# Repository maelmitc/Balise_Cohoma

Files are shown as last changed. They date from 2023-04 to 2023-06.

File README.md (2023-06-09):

# $${\color{black}Balise \space \color{black}Cohoma}$$

* CHARBONNIER Maëna
* MITCHEL Maël
* NGUYEN Denis
* SALOT Robin
* TESTUZ Lauriane

## $${\color{black}Présentation \space \color{black}du \space \color{black}{projet}}$$

Ce projet est en collaboration avec des deuxièmes années qui participent au projet Cohoma, pour l'armée de terre. Ce projet
est une compétition entre différentes écoles d'ingénieurs. Il consiste en la création d'un robot autonome s'adaptant à tout type de terrains. Ce robot doit lâcher des balises sur son chemin, elles ont pour but de le localiser. C'est ce sur quoi nous avons travaillé. 
   
Une LED RGB est utilisée afin de montrer le niveau de batterie de la balise (vert: pleine charge, jaune: à moitié chargée et rouge: déchargée). Quatre LEDs bleues sont également utilisées afin de déterminer le niveau de connexion Internet de la balise. Il y a également un capteur infrarouge qui permet de communiquer avec le rover afin d'allumer la batterie. Enfin, on utilise un convertisseur Buck-Boost, qui est une alimentation à découplage qui convertit une tension continue en une autre tension continue de plus faible ou de plus grande valeur, mais de polarité inverse.

## $${\color{black}Cahier \space \color{black}des \space \color{black}{charges}}$$

* Rendre visible le niveau de batteries de la balise (sur la balise).
* Rendre visible le niveau de réception WIFI de la balise (sur la balise).
* Communication infrarouge entre une télécommande et la balise.
* Communication infrarouge entre le rover et la balise dans le but d'allumer la balise après lors de l'éjection.
* Alimenter la balise.

## $${\color{black}Datasheet}$$

* [Buck / Boost ](https://www.farnell.com/datasheets/1999134.pdf)
* [Diode (Buck) (1N4148)](https://4donline.ihs.com/images/VipMasterIC/IC/DIOD/DIOD-S-A0001754954/DIOD-S-A0001754954-1.pdf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)
* [Diode Schottky (FSV340AF)](https://www.mouser.fr/datasheet/2/308/FSV340AF_D-1810142.pdf)
* [Capteur IR TFBS4650](https://www.vishay.com/docs/84672/tfbs4650.pdf)
* [Interface USB/UART(CY7C64225-28PVXCT)](https://www.mouser.fr/datasheet/2/196/CYPR_S_A0003298042_1-3003715.pdf)
* [Encodeur/Decodeur IrDA MCP2120-I/SL ](https://docs.rs-online.com/4edb/0900766b814ada76.pdf)
* [Quartz pour Encodeur/Decodeur IrDA ABLS-7.3728MHZ-20-B-3-H-T ](https://www.mouser.fr/datasheet/2/3/abls-1664338.pdf)
* [Récepteur IrDA TSOP75338TT](https://www.mouser.fr/datasheet/2/427/tsop753-1767096.pdf)
* [Emetteur IrDA VSML3710-GS18](https://www.mouser.fr/datasheet/2/427/vsml3710-1766511.pdf)
* [Processeur STM32L412KBT6](https://www.mouser.fr/datasheet/2/389/stm32l412c8-1851177.pdf)
* [Quartz pour STM32 ABLS-16.000MHZ-20-B-3-H-T:](https://www.mouser.fr/datasheet/2/3/abls-1664338.pdf)
* [Led bleu (niveau de réception) : MP008276]( https://www.farnell.com/datasheets/3497873.pdf)
* [Led RGB (niveau batterie) : 5988G10313F ](https://www.mouser.fr/datasheet/2/109/C18481B-2944388.pdf)
* [Driver de LED I2C : PCA9685PW,118 ]( https://www.mouser.fr/datasheet/2/302/PCA9685-1127478.pdf)

## $${\color{black}Déroulement \space \color{black}du \space \color{black}{projet}}$$

### Software :

L'objectif du logiciel développé est le traitement des données du routeur et de la batterie et la commande du <em>driver</em> LED. Le code a été développé en C. Le code est implémenté sur un processeur STM32 L412KBT6. En fonction des données reçues, le logiciel commande les LEDs, en particulier en fonction du niveau de batterie disponible. Le driver de LEDs, relié à quatre LEDs bleues et une LED RGB est connecté en I2C avec le processeur STM32.

* [Architecture <em>software</em>](Software/[CoHoMa]BeaconSoftwareArchitecture.drawio) (originale, modifiée depuis)
* [Code](Software/CHMBeaconB.zip)

#### Batterie
Selon le niveau de batterie calculé, 1 à 4 Blue LEDs sont allumées
* 75% : 4 LEDs activées
* 50% : 3 LEDs activées
* 25% : 2 LEDs activées
* 10% : 1 LED activée
On utilise une connexion I²C pour lier le STM32 au <em>driver</em> LED.

#### Routeur/IR
On utilise une LED RGB pour témoigner de la qualité de la connexion.
En fonctionnement normal, on utilise 3 couleurs : rouge (signal faible), vert (signal moyen), bleu (signal fort).

#### Problèmes rencontrés lors du développement :
* Longue lecture des fiches techniques des composants utilisés
* Recherche et étude d'un algorithme pour déterminer le niveau de batterie (SOC Algorithm)
* Lien entre la partie <em>hardware</em> et <em>software</em>, en particulier le lien avec la batterie/le niveau de charge

D'un point de vue personnel, je juge avoir sous-estimé la quantité de travail à fournir dans la partie <em>software</em>, trop importante pour une seule personne.

### Hardware - PCB Leds:

La version finale de mon [PCB](Hardware/PCB_LEDs/PCB_LEDs.kicad_sch_copie.kicad_pro).

#### Composants utilisés : 

Type de produit | Empreinte | Nombre 
--- | --- | ---
Driver de LEDs | Package_STO:TSSOP-28_4.4x9.7mm_P0.65mm | 1
LED bleue | LED_SMD:LED_0603_1608Metric_Pad1.05x0.95mm_HandSolder | 4 
LED RGB | LED_SMD:LED_Avago_PLCC6_3x2.8mm | 1
Résistance (100Ω et 150Ω)| Resistor_SMD:R_0603_1608Metric_Pad0.98x0.95mm_HandSolder | 7
Connecteur 01x05 | Connector_JST:JST_XH_B5B-XH-A_1x05_P2.50mm_Vertical | 1

#### Utilité des composants :

* Driver de LEDs : pilote les LEDs.
* LEDs bleues : montrent le niveau de connexion Wifi sur la balise. Plus le nombre de LEDs allumées est important, plus la connexion internet est bonne. 
* LED RGB : montre le niveau de batterie de la balise. Si la LED est verte, la balise est entièrement chargée ; jaune, à moitié chargée ; rouge, déchargée.
* Résistances : permettent de limiter le courant qui traverse les LEDs.
* Connecteur : permet de faire communiquer le driver de LEDs avec l’extérieur. Il est composé de cinq sorties : une d'alimentation et une de masse, mais également d'une sortie SDA (Serial Data Line), d'une sortie SCL (Serial Clock Line) et d'une sortie output enable, qui permet d’activer ou de désactiver les sorties de LEDs, en fonction des besoins.

#### Choix des résistances : 

Le driver de LEDs est alimenté par une tension de 5V. La tension maximum que peuvent recevoir les LEDs est d’environ 3V. Or, puisqu’on a un courant de 25 mA qui doit traverser les LEDs, on en conclut que la résistance qui doit être ajoutée afin de limiter la tension est de 100Ω. EN ce qui concerne la LED RGB, la diode rouge supporte une tension moins importante que les diodes jaune et verte. Sa résistance doit donc être supérieure à celles des diodes jaune et verte. C’est pourquoi, on ajoute une résistance de 150Ω.

#### Problèmes rencontrés lors de la fabrication de ce PCB : 

En ce qui concerne les LEDs bleues, il n'y a pas de problème, elles s'allument correctement. En revanche, cette partie comporte un principal problème : à cause d'une mauvaise connexion des pins de la LED RGB, on s'est rendu compte que seule la diode verte s'allume, les diodes jaune et rouge ne fonctionnent pas. Il faut prendre garde à ne pas se tromper entre l'anode et la cathode des diodes, pour éviter que l'erreur ne se reproduise. 

### Hardware - PCB IR :

La version finale de mon [PCB](Hardware/PCB_IR/cohoma.kicad_pro).

#### Composants utilisés : 

Type de produit | Empreinte | Nombre 
--- | --- | ---
Décodeur | Package_SO:SOIC-14_3.9x8.7mm_P1.27mm | 1
Récepteur Infrarouge | Package_SO:TSOP753TT (empreinte que nous avons créée) | 1
Quartz | Crystal:Crystal_SMD_7050-2Pin_7.0x5.0mm | 1
Condensateur (20 pF et 100 nF)| Capacitor_SMD:C_0603_1608Metric_Pad1.08x0.95mm_HandSolder | 3
Connecteur 01x03 | Connector_PinHeader_1.27mm:PinHeader_1x03_P1.27mm_Horizontal | 1 

Ce PCB se compose de plusieurs parties:

#### Récepteur IR:
Le récepteur IR reçoit un signal provenant d'un émetteur IR. Il renvoie alors RXIR à l'encodeur/décodeur dans le but que le signal soit décodé.
Afin d'éviter les fluctuations de tensions, il était recommandé par la datasheet, lorsque Vs<2.8 V d'utiliser une résistance et un condensateur. Ce n'est ici pas le cas, cependant, afin d'éviter tout risque, un condensateur de 100 nF a tout de même été ajouté.

#### Encodeur/Décodeur:
Dans le cadre de ce projet, ce composant a été utilisé uniquement comme un décodeur. Il reçoit RXIR, le décode et renvoie UART_RX au microcontrôleur (via le connecteur).
En effet, pour être compris par le microcontrôleur, le signal doit être en UART.

Les "BAUD" permettent de modifier la vitesse de transmission. Ils sont tous les trois mis à la masse ici, ce qui équivaut à les mettre à 0.

#### Quartz:
Le quartz sert d'horloge. Il est ici accompagné de deux condensateurs qui permettent de "lisser" afin que l'horloge soit vraiment régulière.

#### Difficultés rencontrées lors de la fabrication de ce PCB :
* Trouver les schematics correspondants au projet (pour plusieurs composants, elles n'existaient pas sur Kicad: il a donc été nécessaire de les trouver, les télécharger, puis les importer sur Kicad).
* La datasheet du quartz ne permettait pas de connaître la schematic associée, il fallait effectuer d'autres recherches.
* De même pour les empreintes de certains composants, il fallait alors trouver une empreinte très proche, ou bien créer l'empreinte dans certains cas.
* Rendre le PCB le plus petit possible tout en respectant une contrainte: les deux condensateurs associés au Quartz devaient être aussi proche que possible de ce dernier.
* Problèmes rencontrés lors de la soudure liés à une mauvaise empreinte ( qui a été corrigée sur la dernière version du PCB).

### Hardware - PCB Buck-Boost:

La version finale de notre [PCB](Hardware/PCB_BuckBoost/pcb_v3/pcb_v3.kicad_pro).

#### Composants utilisés : 

Type de produit | Empreinte | Nombre 
--- | --- | ---
Diode| Diode_SMD:D_SOD-123F | 1
Diode| Diode_SMD:D_SOD-323F | 1
PS1| Footprints_Balise:PS1 | 1
Régulateur Buck/Boost | Package_SO:SOIC-8-1EP_3.9x4.9mm_P1.27mm_EP2.29x3mm | 2
Condensateur polarisé (330 uF)| Capacitor_SMD:CP_Elec_10x10.5 | 2
Condensateur polarisé (100 uF)| Capacitor_SMD:CP_Elec_6.3x7.7 | 1
Condensateur polarisé (22 uF)| Capacitor_SMD:CP_Elec_5x5.4 | 1
Condensateur (2.2 uF, 1 uF et 0.47 nF)| Capacitor_SMD:C_0603_1608Metric_Pad1.08x0.95mm_HandSolder | 6
LED bleue | LED_SMD:LED_0603_1608Metric_Pad1.05x0.95mm_HandSolder | 4 
Inductance (100 uH)| Inductor_SMD:L_Wuerth_WE-PD-Typ-LS | 2
Résistance | Resistor_SMD:R_0603_1608Metric_Pad0.98x0.95mm_HandSolder | 11
Diode Schottky | Footprints_Balise:Diode_Schottky (empreinte créée)| 2
Connecteur 01x02 | Connector_JST:JST_XH_B2B-XH-A_1x02_P2.50mm_Vertical | 4

#### Utilité des composants
* LEDs bleues : témoignent du bon fonctionnement de l'alimentation
* Diodes / Diode Schottky : permettent les différents états de commutation du régulateur
* Régulateur à découpage : gère le découpage (via le rapport cyclique) de la tension en fonction des différents états. Les régulateurs sont au nombre de deux, chacun est monté différemment, permettant le passage au mode Buck ou Boost.
* PS1 : régule la tension

#### Choix des composants     
Les composants (autre que ceux imposés) ont été sélectionnés en fonction des datasheets des montages Buck et Boost et des composants passifs disponibles à l'ENSEA. Pour ce qui est des condensateurs, des condensateurs classiques ou polarisés ont été choisi en fonction de la valeur des capacités indiquées sur la datasheet (au dessus de 10 uF, on choisit un condensateur polarisé).

#### Explication du fonctionnement des régulateurs à découplage  
Un régulateur de découplage est un type de régulateur de tension qui utilise des composants électroniques commutés (transistors, inductances, condensateurs) pour convertir l'énergie de manière efficace. 

Régulation de la tension d'entrée : Le régulateur de découplage commence par réguler et contrôler la tension d'entrée, celle-ci pouvant être supérieure ou inférieure à la tension de sortie souhaitée, à l'aide de composants électroniques commutés.

Conversion d'énergie : L'énergie est efficacement convertie en utilisant un interrupteur électronique, généralement un transistor, pour commuter rapidement entre les états "on" et "off". Il est possible de réduire les pertes d'énergie et d'améliorer l'efficacité globale du régulateur grâce à cette commutation.

Stockage de l'énergie : Pendant la commutation, l'énergie est stockée dans une inductance (bobine) lors de l'état "on" de l'interrupteur et est libérée lors de l'état "off". Cela permet de réguler et de maintenir la tension de sortie constante malgré les variations de la tension d'entrée ou de la charge.

Filtrage : Le régulateur de découplage utilise également des condensateurs pour filtrer les fluctuations résiduelles de la tension de sortie et pour fournir une alimentation stable et régulée.

#### Difficultés rencontrées lors de la fabrication de ce PCB : 
* Repérer sur la datasheet les montages buck et boost qui correspondaient au projet.
* Choisir des empreintes des condensateurs et des inductances adaptées à la situations (exemple : condensateurs polarisés).
* Assigner (voire créer) les bonnes empreintes car elles n'étaient pas toujours disponibles sur Kicad.  
* Agencer les composants afin d'obtenir un PCB le plus petit possible.
* Placer les composants traversés par une forte tension de manière optimale (ils devaient être proches des régulateurs à découpage).
* Il fallait imposer un courant de sortie de 100 mA, ce qui n'était possible que si la balise était complète. Or, ce n'était pas le cas, puisque nous n'avions que le PCB. Nous avons donc dû rajouter deux résistances en parallèle à un condensateur polarisé.
* Choisir une largeur de piste suffisante en fonction du courant qui traversait les différents composants. 
* Augmenter le nombre de vias car ils ne fonctionnaient pas toujours.
* Certaines pastilles de cuivres n'étaient pas connectés à la masse, une erreur lors de la conception du PCB sur Kicad.

## $${\color{black}Impact \space \color{black}environnemental}$$

### $${\color{green}Expliquer \space \color{green}les \space \color{green}{critères} \space \color{green}de \space \color{green}choix \space \color{green}du \space \color{green}mode \space \color{green}d'alimentation \space \color{green}de \space \color{green}votre \space \color{green}{projet}}$$

Notre projet exigeait déjà un cahier des charges précis à respecter. En effet, la plupart des composants, y compris l'alimentation Buck-Boost, étaient imposés. Cependant, on peut tout de même se demander pourquoi c'est une alimentation à découpage qui à été choisie plutôt qu'une alimentation linéaire. En effet, l'alimentation à découpage possède un rendement bien plus élevé (et consomme donc moins d'énergie) que l'amplificateur linéaire grâce à son fonctionnement "alterné" entre différents états de commutations. Cette meilleure efficacité énergétique est principalement due à leur principe de fonctionnement différent. Dans un régulateur linéaire, la tension excédentaire est dissipée sous forme de chaleur par un transistor de régulation. Cela signifie que la différence de tension entre l'entrée et la sortie du régulateur est convertie en chaleur, ce qui entraîne une perte d'énergie importante. Par conséquent, les régulateurs linéaires ont généralement une efficacité relativement faible, en particulier lorsque la différence de tension entre l'entrée et la sortie est importante. 

En revanche, les régulateurs de découplage utilisent des composants électroniques commutés, tels que des transistors MOSFET et des inductances, pour réguler la tension de sortie. Ces composants commutent rapidement entre les états "on" et "off", ce qui permet de minimiser les pertes d'énergie. Lorsque le transistor est en état "on", il présente une résistance très faible, ce qui réduit les pertes de puissance. Lorsque le transistor est en état "off", l'inductance stocke l'énergie et la restitue lors de l'état "on" suivant, ce qui permet de maintenir une tension de sortie constante.En conséquence, les régulateurs de découplage ont une efficacité énergétique beaucoup plus élevée que les régulateurs linéaires. Une plus grande quantité d'énergie est transférée du côté de l'entrée vers le côté de la sortie sans être dissipée sous forme de chaleur. De plus, en raison du rapport cyclique, le transformateur à l'intérieur de l'alimentation peut être très petit, réalisant ainsi la miniaturisation de la taille de l'alimentation tout en permettant également l'utilisation normale de l'alimentation. 

Il est à noter que dans certains cas (dans d'autres projets par exemple), l'utilisation des régulateurs linéaire est préférable : 
* Moins sensible aux variations de la tension d'entrée,
* Coût moins élevé,
* Meilleure performance en terme de réduction de bruit et des interférences électromagnétique, 
* Moins complexe
* Réglage plus fin de la sortie.

### $${\color{green}Votre \space \color{green}projet \space \color{green}favorise-t-il \space \color{green}une \space \color{green}utilisation \space \color{green}judicieuse \space \color{green}et \space \color{green}rationnelle \space \color{green}de \space \color{green}l'énergie, \space \color{green}en \space \color{green}minimisant \space \color{green}{les}}$$

### $${\color{green}impacts \space \color{green}de \space \color{green}sa \space \color{green}production, \space \color{green}de \space \color{green}sa \space \color{green}distribution \space \color{green}et \space \color{green}de \space \color{green}sa \space \color{green}{consommation?}}$$
 
La plupart des composants étant imposés, nous avons eu peu de marge de manoeuvre. Nous avons donc porté une attention toute particulière à la taille des PCBs conçus. En effet, ces derniers devaient être les plus petits possibles, afin de ne pas gaspiller de matériaux. De plus, les PCBs ayant été réalisés sur place, leur impact environnemental dû aux transports était minime, les composants étant déjà à l'école.
 
Pour ce qui est des LEDs présentes sur le projet, elles ne s’allument que lorsque le module qui leur est associé est sollicité. Ainsi il n'y a pas d'énergie utilisée inutilement. De plus, nous nous sommes assurés qu’aucun composant ne consomme plus d’énergie que celle nécessaire à son bon fonctionnement.

Cependant, si l’on s’intéresse au projet de manière plus large, son impact est plus important que ce que nous avons décrit précédemment. En effet, plusieurs écoles sont en compétition dans la réalisation de ce projet pour ne sélectionner que le meilleur. L’impact aurait été moins important si une seule équipe d’ingénieurs professionnels s’en était chargée. Néanmoins, cette compétition entre écoles encourage chacun des participants à réaliser le projet le plus efficace et propre possible dans l’espoir d’être sélectionnés.

## $${\color{black}Conclusion}$$

Nous avons manqué de temps pour atteindre tous nos objectifs. Cependant, si nous pouvions donner des conseils à nos successeurs, nous dirions de :
 
* Bien lire les datasheet des composants, de façon à choisir des valeurs de résistances ou de condensateurs appropriées, par exemple. 
* Faire particulièrement attention aux empreintes, quitte à en créer, de façon à n'avoir aucun problème lors de la soudure.
* Faire particulièrement attention au sens des diodes, ne pas intervertir l'anode et la cathode, dans le cas ou le PCB en comporte.
* Faire attention à la largeur des pistes, en fonction du courant qui traverse les différents composants.

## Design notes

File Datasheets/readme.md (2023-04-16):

* Battery Management System : https://www.amazon.fr/ZkeeShop-Lithium-Battery-Protection-Discharge/dp/B08F2H2MXG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
* Buck / Boost : https://fr.farnell.com/microchip/mic3172ym/ic-switching-reg-1-25a-100khz/dp/2510055
* Diode (Buck) [1N4148] : https://fr.farnell.com/diodes-inc/1n4148ws-7-f/diodess-commutateur75v0-2wsod323/dp/1843678
* Diode Schottky [FSV340AF] : https://www.mouser.fr/datasheet/2/308/FSV340AF_D-1810142.pdf
* Condensateur / Inductance : https://www.we-online.com/en
* Capteur IR TFBS4650 : https://www.vishay.com/docs/84672/tfbs4650.pdf
* Interface USB/UART [CY7C64225-28PVXCT]: https://www.mouser.fr/datasheet/2/196/CYPR_S_A0003298042_1-3003715.pdf
* Encodeur/Decodeur IrDA MCP2120-I/SL : https://docs.rs-online.com/4edb/0900766b814ada76.pdf
* Quartz pour Encodeur/Decodeur IrDA ABLS-7.3728MHZ-20-B-3-H-T : https://www.mouser.fr/datasheet/2/3/abls-1664338.pdf
* Récepteur IrDA TSOP75338TT: https://www.mouser.fr/datasheet/2/427/tsop753-1767096.pdf
* Emetteur IrDA VSML3710-GS18: https://www.mouser.fr/datasheet/2/427/vsml3710-1766511.pdf
* Processeur STM32L412KBT6: https://www.mouser.fr/datasheet/2/389/stm32l412c8-1851177.pdf
* Quartz pour STM32 ABLS-16.000MHZ-20-B-3-H-T: https://www.mouser.fr/datasheet/2/3/abls-1664338.pdf
* Led bleu (niveau de réception) : MP008276 : https://www.farnell.com/datasheets/3497873.pdf
* Led RGB (niveau batterie) : 5988G10313F : https://www.mouser.fr/datasheet/2/109/C18481B-2944388.pdf
* Driver de LED I2C : PCA9685PW,118 : https://www.mouser.fr/datasheet/2/302/PCA9685-1127478.pdf

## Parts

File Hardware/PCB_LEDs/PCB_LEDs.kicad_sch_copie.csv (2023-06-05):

Source: | C:\Users\Lolo1\OneDrive\Documents\Github\Balise_Cohoma\Hardware\PCB_LEDs\PCB LEDs.kicad_sch_copie.kicad_sch
Date: | 15/05/2023 18:41:45
Tool: | Eeschema 7.0.1
Generator: | C:\Program Files\KiCad\7.0\bin\scripting\plugins/bom_csv_grouped_by_value.py
Component Count: | 18
Collated Components:
Item | Qty | Reference(s) | Value | LibPart | Footprint | Datasheet | DNP
1 | 1 | D1 | LED_RGB | Device:LED_RGB | LED_SMD:LED_Avago_PLCC6_3x2.8mm | ~
2 | 1 | D2 | LED_1 | Device:LED_Small | LED_SMD:LED_0603_1608Metric_Pad1.05x0.95mm_HandSolder | ~
3 | 1 | D3 | LED_2 | Device:LED_Small | LED_SMD:LED_0603_1608Metric_Pad1.05x0.95mm_HandSolder | ~
4 | 1 | D4 | LED_3 | Device:LED_Small | LED_SMD:LED_0603_1608Metric_Pad1.05x0.95mm_HandSolder | ~
5 | 1 | D5 | LED_4 | Device:LED_Small | LED_SMD:LED_0603_1608Metric_Pad1.05x0.95mm_HandSolder | ~
6 | 4 | H1, H2, H3, H4 | MountingHole_Pad | Mechanical:MountingHole_Pad | MountingHole:MountingHole_3.2mm_M3_DIN965_Pad | ~
7 | 1 | J1 | Conn_01x05 | Connector_Generic:Conn_01x05 | Connector_JST:JST_XH_B5B-XH-A_1x05_P2.50mm_Vertical | ~
8 | 6 | R1, R2, R3, R4, R5, R6 | 100 | Device:R_Small | Resistor_SMD:R_0603_1608Metric_Pad0.98x0.95mm_HandSolder | ~
9 | 1 | R7 | 150 | Device:R_Small | Resistor_SMD:R_0603_1608Metric_Pad0.98x0.95mm_HandSolder | ~
10 | 1 | U1 | PCA9685PW | Driver_LED:PCA9685PW | Package_SO:TSSOP-28_4.4x9.7mm_P0.65mm | http://www.nxp.com/documents/data_sheet/PCA9685.pdf

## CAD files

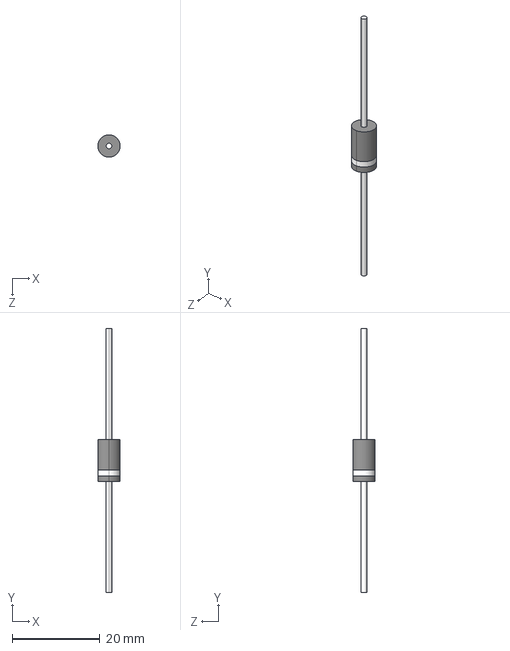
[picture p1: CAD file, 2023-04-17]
Hardware/PCB_BuckBoost/Footprints_Balise/1N5822.step
5.08 x 60.3 x 5.08 mm

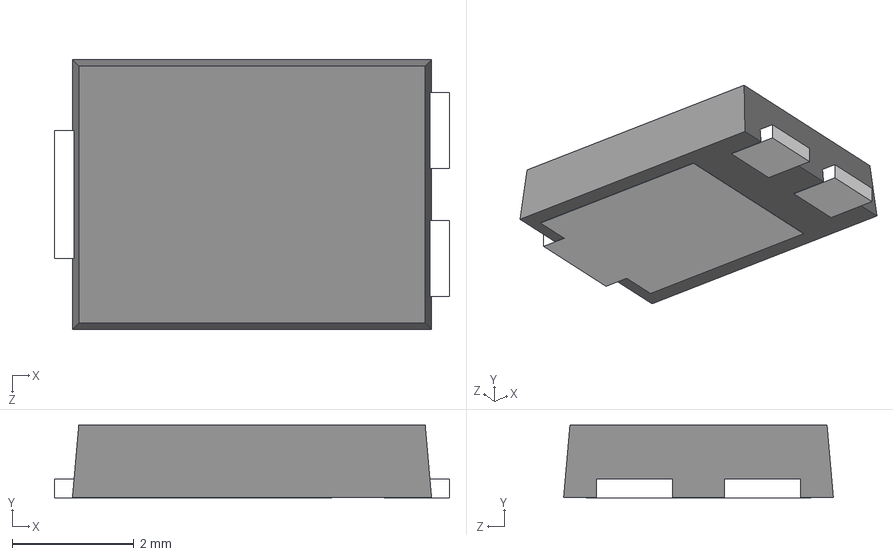
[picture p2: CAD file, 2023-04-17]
Hardware/PCB_BuckBoost/Footprints_Balise/TO-277.step
6.50 x 1.20 x 4.44 mm

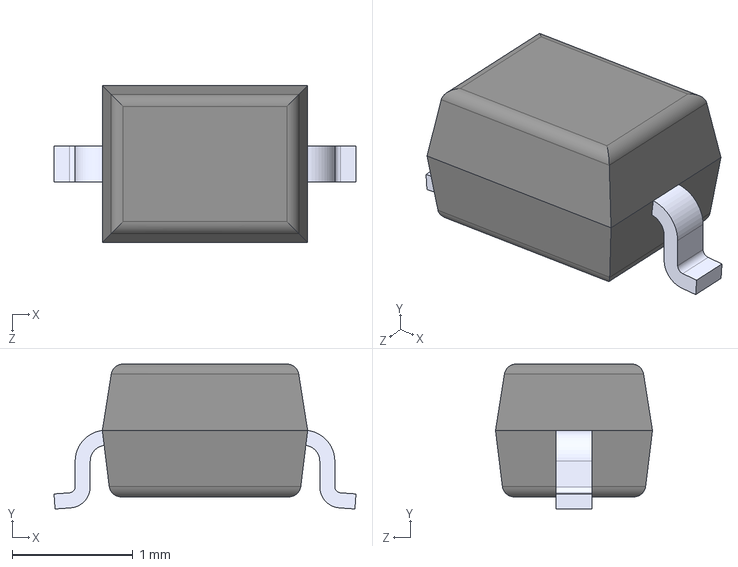
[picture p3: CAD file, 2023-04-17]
Hardware/PCB_BuckBoost/Footprints_Balise/1N4148WS-7-F.step
2.50 x 1.20 x 1.30 mm

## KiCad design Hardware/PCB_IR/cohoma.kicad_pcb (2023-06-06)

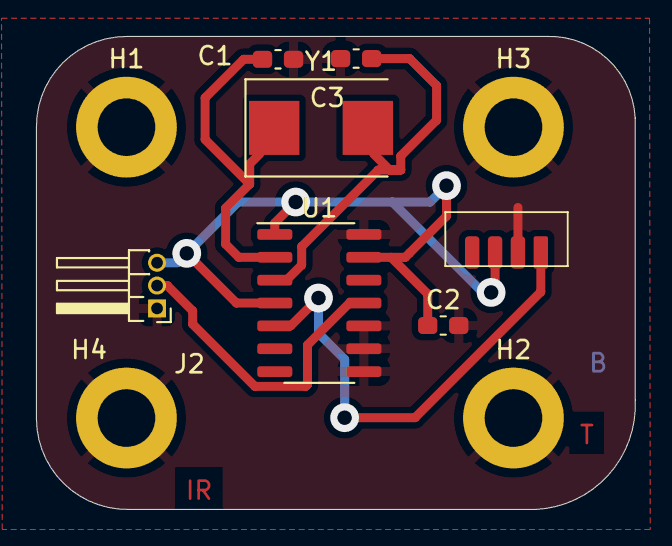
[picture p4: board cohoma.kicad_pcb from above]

Board: 2 copper layers, 33.3 x 26.3 mm, 11 parts (0 on the bottom side), 5 nets.

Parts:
C1, C3: 20 pF; C_0603_1608Metric_Pad1.08x0.95mm_HandSolder
C2: 100 nF; C_0603_1608Metric_Pad1.08x0.95mm_HandSolder
H1: Mounting Hole 1; MountingHole_3.2mm_M3_DIN965_Pad
H2: Mounting Hole 2; MountingHole_3.2mm_M3_DIN965_Pad
H3: Mounting Hole 3; MountingHole_3.2mm_M3_DIN965_Pad
H4: Mounting Hole 4; MountingHole_3.2mm_M3_DIN965_Pad
J2: Conn_01x03; PinHeader_1x03_P1.27mm_Horizontal
U1: MCP2120-I/P; SOIC-14_3.9x8.7mm_P1.27mm
U2: TSOP75338WTT; TSOP753TT
Y1: ABLS-7.3728MHz-20-B-3-H-T; Crystal_SMD_7050-2Pin_7.0x5.0mm

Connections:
+3.3V: C2.1, J2.3, U1.1 (VDD), U1.4 (*RESET), U1.13 (EN)
GND: C1.2, C2.2, C3.2, H1.1, H2.1, H3.1, H4.1, J2.1, U1.8 (BAUD2), U1.9 (BAUD1), U1.10 (BAUD0), U1.14 (VSS)
Q_IN: C1.1, U1.2 (OSC1/CLKIN), Y1.1
Q_OUT: C3.1, U1.3 (OSC2), Y1.2
UART_RX: J2.2, U1.11 (RX)

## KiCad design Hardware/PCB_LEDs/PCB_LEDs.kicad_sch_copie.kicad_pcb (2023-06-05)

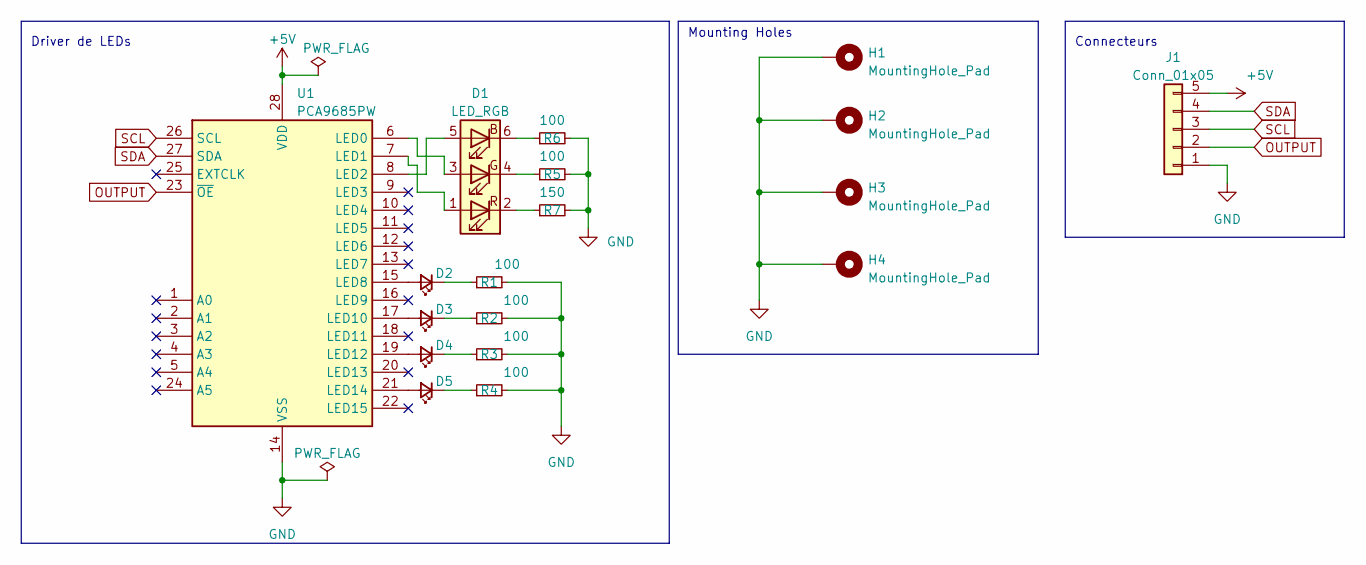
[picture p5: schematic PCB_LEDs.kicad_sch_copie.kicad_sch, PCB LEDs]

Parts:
D1: LED_RGB; LED_Avago_PLCC6_3x2.8mm
D2: LED_1; LED_0603_1608Metric_Pad1.05x0.95mm_HandSolder
D3: LED_2; LED_0603_1608Metric_Pad1.05x0.95mm_HandSolder
D4: LED_3; LED_0603_1608Metric_Pad1.05x0.95mm_HandSolder
D5: LED_4; LED_0603_1608Metric_Pad1.05x0.95mm_HandSolder
H1, H2, H3, H4: MountingHole_Pad; MountingHole_3.2mm_M3_DIN965_Pad
J1: Conn_01x05; JST_XH_B5B-XH-A_1x05_P2.50mm_Vertical
R1, R2, R3, R4, R5, R6: 100; R_0603_1608Metric_Pad0.98x0.95mm_HandSolder
R7: 150; R_0603_1608Metric_Pad0.98x0.95mm_HandSolder
U1: PCA9685PW; TSSOP-28_4.4x9.7mm_P0.65mm

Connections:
+5V: J1.5, U1.28 (VDD)
GND: H1.1, H2.1, H3.1, H4.1, J1.1, R1.2, R2.2, R3.2, R4.2, R5.2, R6.2, R7.2, U1.14 (VSS)
unnamed: D1.5 (BA), U1.8 (LED2)
unnamed: D1.4 (GK), R5.1
unnamed: D1.6, R6.1
unnamed: D1.1 (RA), U1.7 (LED1)
unnamed: D1.2 (RK), R7.1
unnamed: D2.2 (A), U1.15 (LED8)
unnamed: D2.1 (K), R1.1
unnamed: D3.2 (A), U1.17 (LED10)
unnamed: D3.1 (K), R2.1
unnamed: D4.2 (A), U1.19 (LED12)
unnamed: D4.1 (K), R3.1
unnamed: D5.2 (A), U1.21 (LED14)
unnamed: D5.1 (K), R4.1
unnamed: D1.3 (GK), U1.6 (LED0)
OUTPUT: J1.2, U1.23 (~OE)
SCL: J1.3, U1.26 (SCL)
SDA: J1.4, U1.27 (SDA)

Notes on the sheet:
Connecteurs
Mounting Holes
Driver de LEDs

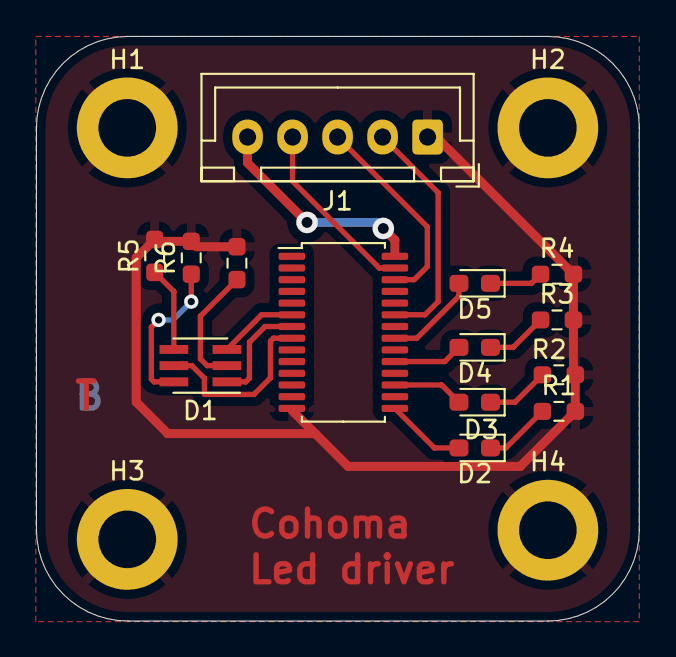
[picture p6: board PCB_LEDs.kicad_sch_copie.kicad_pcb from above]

Board: 2 copper layers, 33.5 x 32.5 mm, 18 parts (0 on the bottom side), 19 nets.

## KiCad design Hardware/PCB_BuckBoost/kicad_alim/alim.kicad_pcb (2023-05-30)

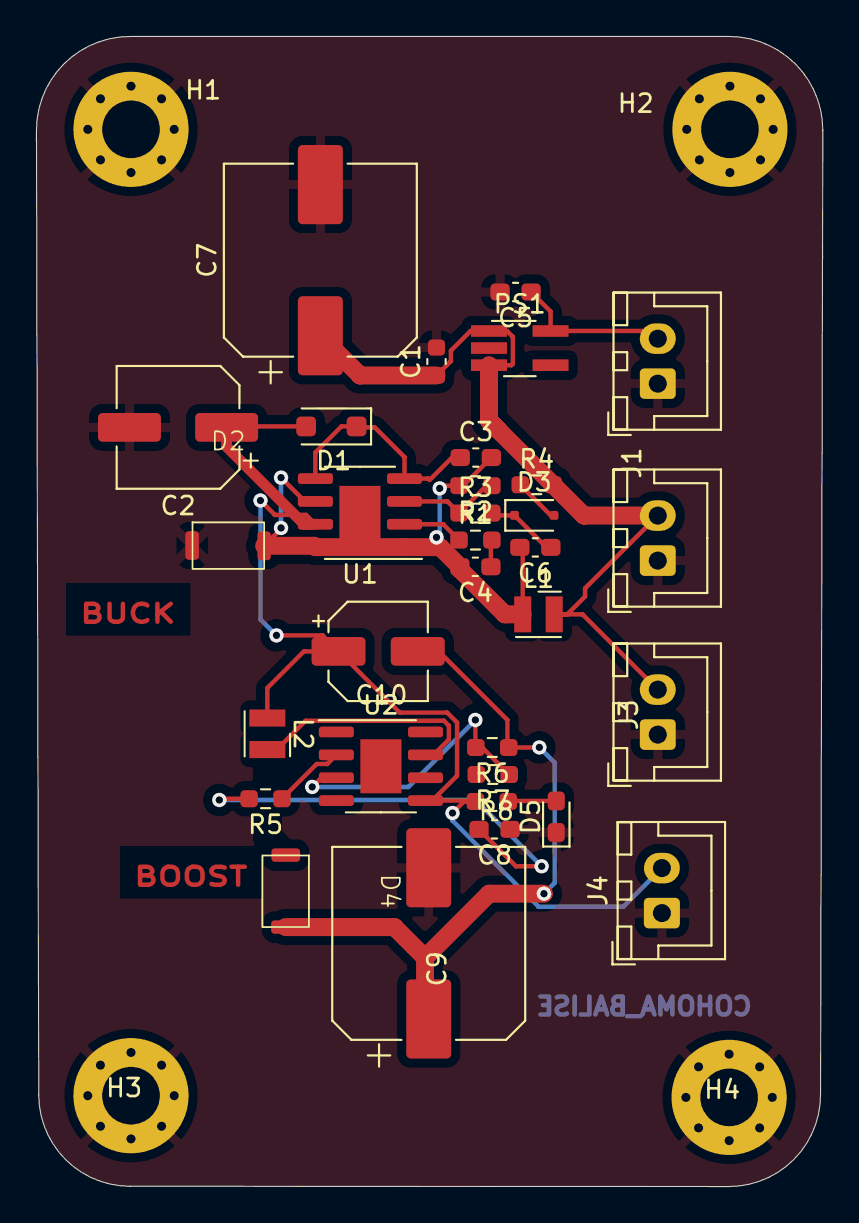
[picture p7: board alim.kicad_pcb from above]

Board: 2 copper layers, 43.7 x 63.9 mm, 36 parts (0 on the bottom side), 16 nets.

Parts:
C1: 0.47u; C_0603_1608Metric
C2: 100uF; CP_Elec_6.3x7.7
C3: 2.2 µF; C_0603_1608Metric_Pad1.08x0.95mm_HandSolder
C4, C6: 1 µF; C_0603_1608Metric_Pad1.08x0.95mm_HandSolder
C5: 0.47u; C_0603_1608Metric_Pad1.08x0.95mm_HandSolder
C7: 330uF; CP_Elec_10x10.5
C8: 1µF; C_0603_1608Metric_Pad1.08x0.95mm_HandSolder
C9: 470uF; CP_Elec_10x10.5
C10: 22uF; CP_Elec_5x5.4
D1: 1N4148; D_SOD-123F
D2, D4: FSV330AF; Diode_Shottky (copy)
D3: 1N4148; D_SOD-323F
D5: LED; LED_0603_1608Metric_Pad1.05x0.95mm_HandSolder
H1, H2, H3, H4: MountingHole_Pad; MountingHole_3.2mm_M3_Pad_Via
J1, J2, J3, J4: Conn_01x02; JST_XH_B2B-XH-A_1x02_P2.50mm_Vertical
L1: 100 µH; L_Wurth_WE-LQSH-2512
L2: 27 µH; L_Wurth_WE-LQSH-2512
PS1: BU33SD5WG-TR; TSOT-23-5_HandSoldering
R1: 470; R_0603_1608Metric_Pad0.98x0.95mm_HandSolder
R2: 1.2 k; R_0603_1608Metric_Pad0.98x0.95mm_HandSolder
R3: 3.7k; R_0603_1608Metric_Pad0.98x0.95mm_HandSolder
R4: 10Ω; R_0603_1608Metric_Pad0.98x0.95mm_HandSolder
R5, R8: 1k; R_0603_1608Metric_Pad0.98x0.95mm_HandSolder
R6: 10.7; R_0603_1608Metric_Pad0.98x0.95mm_HandSolder
R7: 1.24k; R_0603_1608Metric_Pad0.98x0.95mm_HandSolder
U1, U2: MIC3172YM; SOIC-8-1EP_3.9x4.9mm_P1.27mm_EP2.29x3mm

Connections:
+3.3V: C5.1, J1.2, PS1.5 (VOUT)
+5V: C1.1, C7.1, J2.2, J3.2, L1.2, PS1.1 (VIN), PS1.3 (STBY), R4.2
+15V: C2.1, C10.1, D1.2 (A), J4.2, L2.1, R8.1, U1.7 (VSW), U2.5 (VIN)
GND: C1.2, C2.2, C5.2, C7.2, C8.1, C9.2, D2.2 (A), D5.1 (K), H1.1, H2.1, H3.1, H4.1, J1.1, J2.1, J3.1, J4.1, PS1.2 (GND), R7.2, U2.1 (SGND), U2.6 (PGND2), U2.8 (PGND1)
unnamed: C4.1, R1.2
unnamed: C8.2, R5.2
unnamed: C3.1, D1.1 (K), U1.4 (SYNC/EN), U1.5 (VIN)
unnamed: C3.2, C4.2, C6.2, D2.1 (K), L1.1, R1.1, R2.2, U1.1 (SGND), U1.2 (COMP), U1.6 (PGND2), U1.8 (PGND1), U1.9
unnamed: D3.2 (A), R4.1
unnamed: C6.1, D3.1 (K), R3.2
unnamed: D4.2 (A), L2.2, U2.7 (VSW)
unnamed: D5.2 (A), R8.2
unnamed: R2.1, R3.1, U1.3 (FB)
unnamed: R5.1, U2.2 (COMP)
unnamed: R6.2, R7.1, U2.3 (FB)
Routeur: C9.1, C10.2, D4.1 (K), R6.1

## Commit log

2023-04-15 schema Kicad des montages Buck et Boost
    [alim.kicad_sch]
2023-04-16 Modifs des conflits
    Il y avait des éléments qui avaient les mêmes noms dans le buck et dans le boost du coup ça causait des erreurs
    [alim.kicad_sch]
2023-04-16 Correction des autres erreurs
    [alim.kicad_sch]
2023-04-16 Ajouts des autres fichiers
2023-04-16 Footprint assignée
    Je suis vraiment pas sur pour la diode Shottky
    [alim.kicad_sch]
2023-04-16 PCB Boost
    J'ai essayer d'avoir le moins le fils longs possible
    [alim.kicad_pcb]
2023-04-16 FIN PCB BOOST
    Normalement jme suis occupé de l'association de tous les composants et je t'ai fait de la place sur la partie basse du PCB pour le buck
    Hésite pas a modifié la taille ou d'autres truc si ça te convient mieux
    [alim.kicad_pcb]
2023-04-16 Create Cahier des charges
2023-04-16 Footprints des diodes à importer
    [1N4148WS-7-F.step, 1N5822.step, TO-277.step]
2023-04-16 Routage de la partie Boost incomplet car il y a un problème avec les librairies de la diode et du MIC, à reprendre depuis un ordinateur de l'Ensea
    [1N4148WS-7-F.step, 1N5822.step, PCB LEDs.kicad_sch_copie.csv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]
2023-04-17 Add files via upload
    Software Architecture (C/Assembly)
2023-04-17 Complete Software Architecture
    Beacon Software Architecture in C/Assembly (Including the use of interrupts and flags)
2023-04-17 PCB BOOST + RectifIcation FOOTPRINTS
    Je ne suis toujours pas sur des footprints surtout pour la diode D1
2023-04-17 pcb revue
    [PCB LEDs.kicad_sch_copie (copy).kicad_pcb, PCB LEDs.kicad_sch_copie.kicad_pcb, PCB LEDs.kicad_sch_copie.kicad_sch]
2023-04-17 PCB IR
    [cohoma.kicad_sch]
2023-04-17 PCB IR (le bon)
    [cohoma.kicad_sch]
2023-04-17 Réorganisation
    [1N4148WS-7-F.step, 1N5822.step, TO-277.step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]
2023-04-17 Correction des erreurs après amphi
    [PCB LEDs.kicad_sch_copie.csv, PCB LEDs.kicad_sch_copie.kicad_pcb, PCB LEDs.kicad_sch_copie.kicad_sch]
2023-05-01 renommage des datasheets et assignation d'empreintes du Buck/Boost
    [PCB LEDs.kicad_sch_copie.kicad_pcb, PCB LEDs.kicad_sch_copie.kicad_sch, cohoma.kicad_pcb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]
2023-05-01 Update PCB
2023-05-01 mise au propre fichier PCB_BuckBoost et début du routage
    [1N4148WS-7-F.step, 1N5822.step, TO-277.step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]
2023-05-01 pcb presque terminé (3 erreurs)
    [alim.kicad_pcb]
2023-05-02 j'ai corrigé les erreurs dans le pcb
    [alim.kicad_pcb]
2023-05-09 changement du schéma Buck/Boost car erreur
    [alim.kicad_sch]
2023-05-09 PCB avec titre
    [PCB LEDs.kicad_sch_copie.kicad_pcb]
2023-05-09 Footprint Diode Shottky
    [alim.kicad_sch]
2023-05-09 assignation d'empreintes
    [alim.kicad_sch]
2023-05-09 Réparé ?
    [PCB LEDs.kicad_sch_copie.kicad_pcb, alim.kicad_sch]
2023-05-09 Est ce que ca va marcher sur le pc de Maël ?
2023-05-09 début du routage pcb
    [alim.kicad_pcb]
2023-05-09 routage pcb
    [alim.kicad_pcb, alim.kicad_sch]
2023-05-09 routage Buck quasi terminé
    [alim.kicad_pcb]
2023-05-09 PCB BUCK/BOOST
    [alim.kicad_pcb]
2023-05-15 add board buck boost
    [pcb_v2.kicad_pcb]
2023-05-15 version finale
    [cohoma.kicad_pcb]
2023-05-15 Version vraiment finale
    [cohoma.kicad_pcb]
2023-05-15 PCB Final en avancement
    [alim.kicad_pcb, alim.kicad_sch]
2023-05-16 PCB presque fini (manque les liaisons)
    [alim.kicad_pcb]
2023-05-16 Correction erreurs V2
    [PCB LEDs.kicad_sch_copie (copy).kicad_pcb, PCB LEDs.kicad_sch_copie.csv, PCB LEDs.kicad_sch_copie.kicad_pcb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]
2023-05-22 pcb v1 buck boost
    [alim.kicad_pcb, pcb_v2.kicad_pcb, pcb_v3.kicad_pcb]
2023-05-22 PCB V3 presque fini (il manque quelques tracks)
    [pcb_v3.kicad_pcb, pcb_v3.kicad_sch]
2023-05-23 PCB_VB (il reste une erreur au niveau du F.cu)
    [pcb_v3.kicad_pcb, pcb_v3.kicad_sch]
2023-05-23 PCB V3 fini
    [pcb_v3.kicad_pcb]
2023-05-23 pcb sans erreurs (mais avec track à 0.3)
    [cohoma.kicad_pcb, cohoma.kicad_sch]
2023-05-23 pcb avec tracks à 5 mm
    [cohoma.kicad_pcb]
2023-05-23 PCB V3 VRAIMENT FINI
    [pcb_v2.kicad_pcb, pcb_v3.kicad_pcb]
2023-05-23 pcb fini
    [cohoma.kicad_pcb]
2023-05-30 ajout des problèmes sur les PCBs
2023-06-09 Update README.md partie alim et questions de dvpt durable
2023-06-09 Update README.md
    Description de la partie développement/logiciel complétée
